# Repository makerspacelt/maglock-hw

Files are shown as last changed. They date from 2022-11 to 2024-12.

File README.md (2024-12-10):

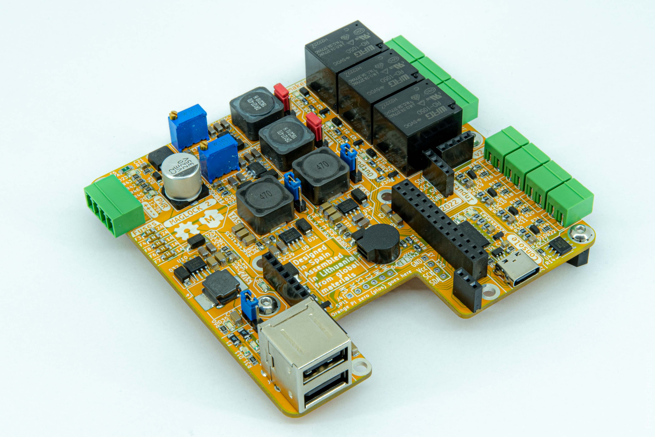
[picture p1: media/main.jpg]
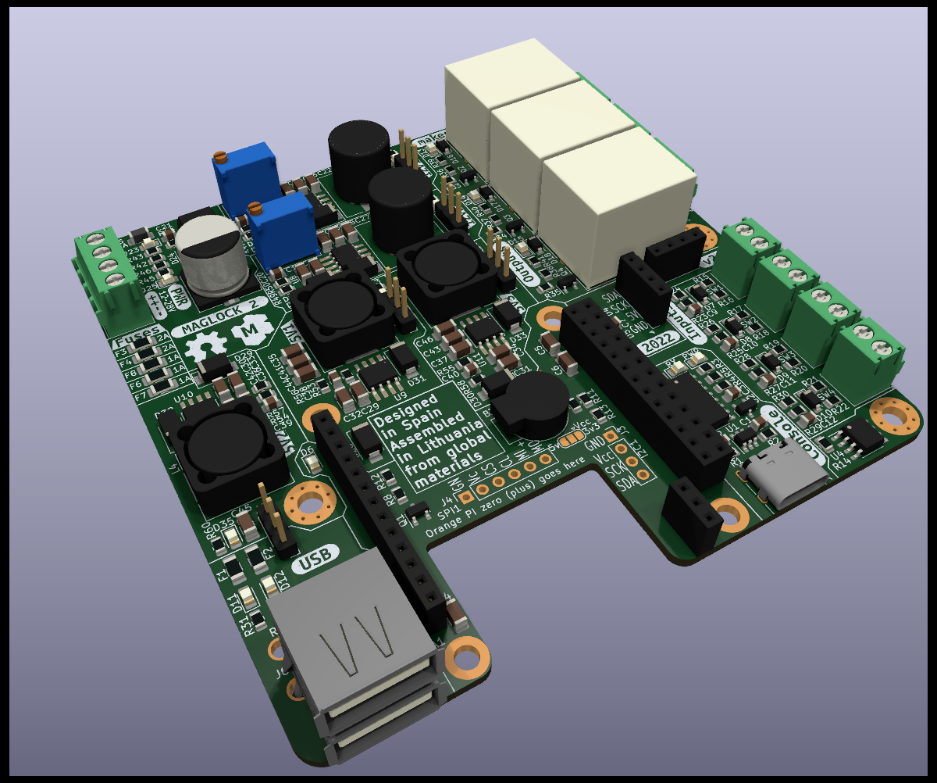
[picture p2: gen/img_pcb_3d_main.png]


MagLock is the entrance controller hardware. It features:

* 2 USB ports for RFID readers
* 3 outputs to electrically controll door (for example, lock/unlock and open/close)
* 4 inputs for normally open switches (for example, doorbell, inside exit button, door position endstops)
* 100Mbps Ethernet for comunication
* onboard UART USB adapter for easy debuging
* onboard DS18B20 1-wire thermometer
* optional I2C oled screen
* additional I2C and SPI breakout for expansion

### Dev NOTEs

* before commit, run `./kibot.sh` to regenerate documentation, bom, gerbers and other assets.
* before fixes after release, bump the version including qr code to next odd value
* before release, bump version to next even value on:
  * every page of schematics and pcb
  * label on front silkscreen
  * qr-code link on bottom silkscreen

* [schematics.pdf](gen/schematics.pdf)
* [pcb.pdf](gen/pcb.pdf)
* [ibom.html](gen/bom_ibom.html)
* [gerbers.zip](gen/gerbers/gerbers.zip)

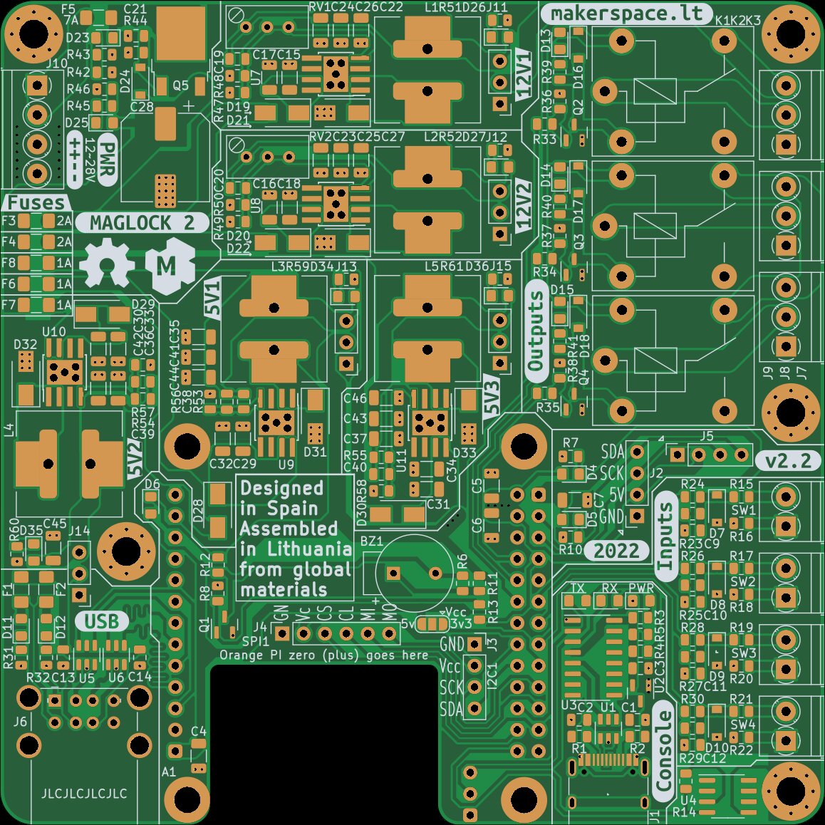
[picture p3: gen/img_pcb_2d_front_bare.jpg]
PCB 2d front bare

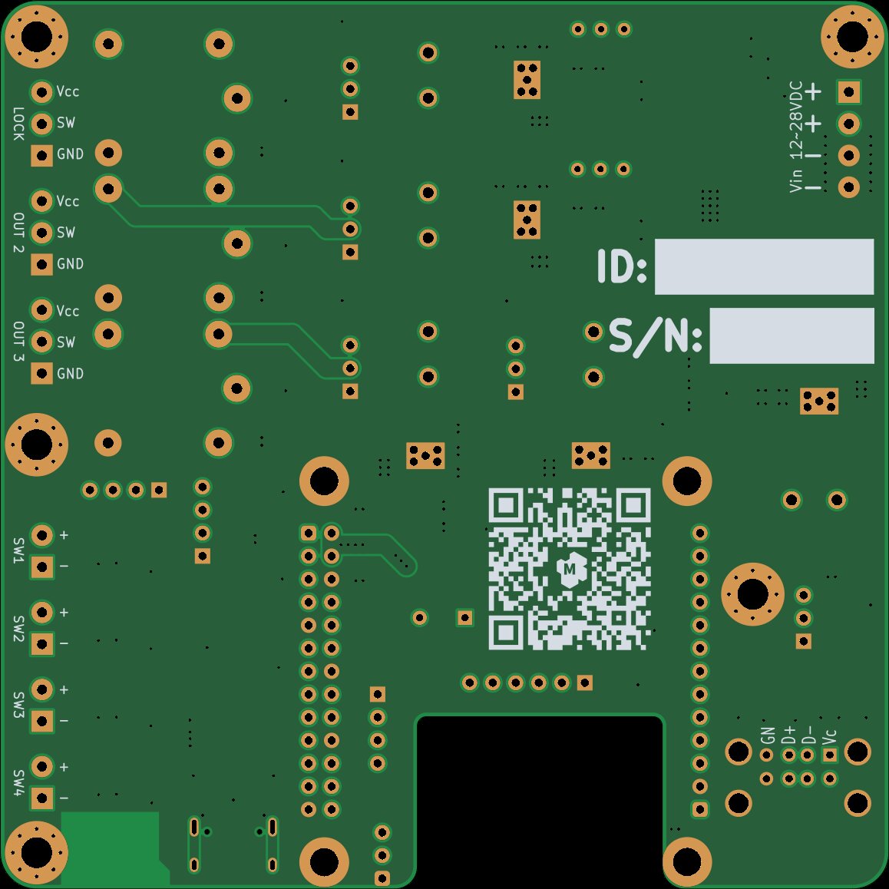
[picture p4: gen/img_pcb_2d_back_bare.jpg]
PCB 2d back bare


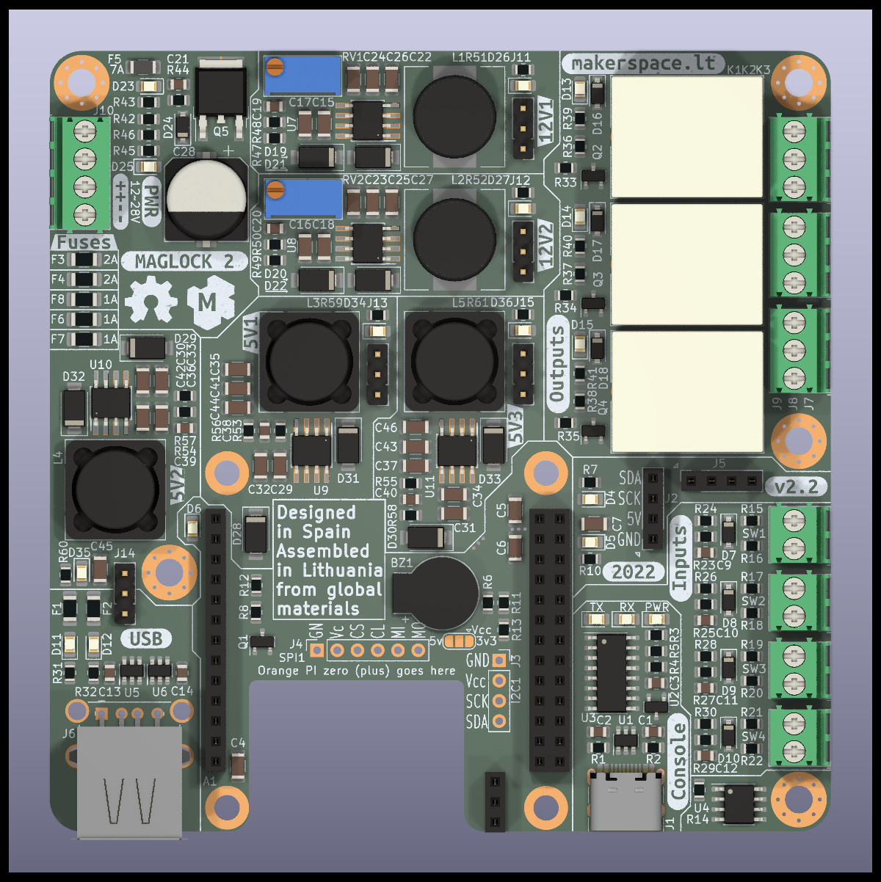
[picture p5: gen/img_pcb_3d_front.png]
PCB 3d front


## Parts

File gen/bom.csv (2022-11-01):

Row | Description | Part | References | Value | Footprint | Quantity Per PCB | Status | Datasheet | LCSC Part Number | WE
1 |  | orange-pi-zero | A1 | orange-pi-zero | Orange_Pi_Zero_LTS | 1 |  | ~ | -
2 | Buzzer, polarized | Buzzer | BZ1 | Buzzer | MagneticBuzzer_CUI_CST-931RP-A | 1 |  | https://datasheet.lcsc.com/lcsc/1810191428_INGHAi-GMD9505RB-3V2700_C252935.pdf | C252935
3 | Unpolarized capacitor | C | C2,C9,C10,C11,C12,C13,C14,C19,C20,C21,C38,C39,C40 | 100n | C_0805_2012Metric | 13 |  | ~ | C161260
4 | Unpolarized capacitor | C | C4,C5,C6,C7,C35,C36,C37,C41,C42,C43,C44,C45,C46 | 100u/10v | C_1206_3216Metric | 13 |  | https://datasheet.lcsc.com/lcsc/1811061115_Murata-Electronics-GRM31CR61A107ME05L_C312983.pdf | C312983 | 885012108012
5 | Unpolarized capacitor | C | C1,C3 | 10u/16v | C_0805_2012Metric | 2 |  | ~ | C77075
6 | Unpolarized capacitor | C | C15,C16,C17,C18,C22,C23,C24,C25,C26,C27,C29,C30,C31,C32,C33,C34 | 10u/35v | C_1206_3216Metric | 16 |  | ~ | C92797 | 885012108022
7 | Polarized capacitor | C_Polarized | C28 | 220u/35v | CP_Elec_10x10 | 1 |  | ~ | C249503 | 875075661007
8 | Zener diode | D_Zener | D7,D8,D9,D10,D24 | 10V | D_SOD-123 | 5 |  | https://datasheet.lcsc.com/lcsc/1806070724_ST-Semtech-MM1Z5240B_C118715.pdf | C118715
9 | 75V 0.15A Fast Switching Diode, SOD-123 | 1N4148W | D16,D17,D18 | 1N4148WL | D_SOD-123 | 3 |  | https://www.vishay.com/docs/85748/1n4148w.pdf | C2908120
10 | Light emitting diode, small symbol, filled shape | LED_Small_Filled | D6,D23 | BLUE | LED_0805_2012Metric_Pad1.15x1.40mm_HandSolder | 2 |  | ~ | C965817
11 | Light emitting diode, small symbol, filled shape | LED_Small_Filled | D2,D3,D13,D14,D15 | GREEN | LED_0805_2012Metric_Pad1.15x1.40mm_HandSolder | 5 |  | ~ | C965815
12 | Light emitting diode, small symbol, filled shape | LED_Small_Filled | D1,D5 | ORANGE | LED_0805_2012Metric_Pad1.15x1.40mm_HandSolder | 2 |  | ~ | C965813
13 | Light emitting diode, small symbol, filled shape | LED_Small_Filled | D4,D11,D12,D34,D35,D36 | RED | LED_0805_2012Metric_Pad1.15x1.40mm_HandSolder | 6 |  | ~ | C965812
14 | 40V 3A Schottky Barrier Rectifier Diode, SMA(DO-214AC) | CDBA340-HF | D19,D20,D21,D22,D28,D29,D30,D31,D32,D33 | SS34A | D_SMA | 10 |  | https://datasheet.lcsc.com/lcsc/2204281430_Guangdong-Hottech-SS34A_C2886580.pdf | C2886580
15 | Light emitting diode, small symbol, filled shape | LED_Small_Filled | D25,D26,D27 | YELLOW | LED_0805_2012Metric_Pad1.15x1.40mm_HandSolder | 3 |  | ~ | C965814
16 | Fuse | Fuse | F6,F7,F8 | 1A | Fuse_1206_3216Metric_Pad1.42x1.75mm_HandSolder | 3 |  | https://datasheet.lcsc.com/lcsc/1912111437_Littelfuse-0466001-NRHF_C151135.pdf | C151135
17 | Fuse | Fuse | F3,F4 | 2A | Fuse_1206_3216Metric_Pad1.42x1.75mm_HandSolder | 2 |  | https://datasheet.lcsc.com/lcsc/1810111821_Littelfuse-0466002-NR_C187595.pdf | C187595
18 | Fuse | Fuse | F5 | 7A | L_1206_3216Metric_Pad1.42x1.75mm_HandSolder | 1 |  | https://datasheet.lcsc.com/lcsc/1809211128_Shenzhen-JDT-Fuse-JFC1206-1700FS_C136352.pdf | C136352
19 | Fuse | Fuse | F1,F2 | PTC 300mA | Fuse_1206_3216Metric_Pad1.42x1.75mm_HandSolder | 2 |  | ~ | C2830239
20 | Generic connector, single row, 01x03, script generated (kicad-library-utils/schlib/autogen/connector/) | Conn_01x03_Male | J11,J12,J13,J14,J15,XJ7,XJ8,XJ9 | 12V_1 | PinHeader_1x03_P2.54mm_Vertical | 8 |  | ~ | ~ C400542
21 | Generic connector, single row, 01x03, script generated (kicad-library-utils/schlib/autogen/connector/) | Conn_01x03_Female | J7,J8,J9 | 3pin | TerminalBlock_Phoenix_PT-1,5-3-3.5-H_1x03_P3.50mm_Horizontal | 3 |  | https://datasheet.lcsc.com/lcsc/1912111437_JILN-JL15EDGRC-35003G01_C409116.pdf | C409116
22 | Generic connector, single row, 01x04, script generated (kicad-library-utils/schlib/autogen/connector/) | Conn_01x04_Female | J2 | I2C0_128x32 | oled_i2c_128x32_ssd1306 | 1 |  | ~ | ~
23 | Generic connector, single row, 01x04, script generated (kicad-library-utils/schlib/autogen/connector/) | Conn_01x04_Female | J5 | I2C0_128x64 | oled_i2c_128x64_ssd1306 | 1 |  | ~ | ~
24 | Generic connector, single row, 01x04, script generated (kicad-library-utils/schlib/autogen/connector/) | Conn_01x04_Female | J3 | I2C1 | PinSocket_1x04_P2.54mm_Vertical | 1 |  | ~ | ~
25 | Generic connector, single row, 01x04, script generated (kicad-library-utils/schlib/autogen/connector/) | Conn_01x04_Female | J10 | Power IN | TerminalBlock_Phoenix_PT-1,5-4-3.5-H_1x04_P3.50mm_Horizontal | 1 |  | https://datasheet.lcsc.com/lcsc/1912111437_JILN-JL15EDGRC-35004G01_C409117.pdf | C409117
26 | Generic connector, single row, 01x06, script generated (kicad-library-utils/schlib/autogen/connector/) | Conn_01x06_Female | J4 | SPI1 | PinSocket_1x06_P2.54mm_Vertical | 1 |  | ~ | ~
27 | USB Type A connector, stacked | USB_A_Stacked | J6 | USB | USB_A_Wuerth_61400826021_Horizontal_Stacked | 1 |  | https://datasheet.lcsc.com/lcsc/2008122034_XUNPU-USB-269-BRW_C720548.pdf | C720548
28 | USB 2.0-only Type-C Receptacle connector | USB_C_Receptacle_USB2.0 | J1 | USB_UART | USB_C_Receptacle_HRO_TYPE-C-31-M-12 | 1 |  | https://datasheet.lcsc.com/lcsc/2205251630_Korean-Hroparts-Elec-TYPE-C-31-M-12_C165948.pdf | C165948
29 | FINDER 36.11, SPDT relay, 10A | FINDER-36.11 | K1,K2,K3 | 5V Relay | Relay_SPDT_Finder_36.11 | 3 |  | https://datasheet.lcsc.com/lcsc/1912111437_WRG-Wangrong-RD-105D_C224434.pdf | C224434
30 | Inductor | L | L1,L2,L3,L4,L5 | 47u/2.5A | L_12x12mm_H8mm__D11.0_P5.0_universal | 5 |  | https://datasheet.lcsc.com/lcsc/2201121400_SHOU-HAN-CYH127-47UH_C2929503.pdf | C2929503 | 744770147
31 | 30V Vds, 5.7A Id, N-Channel MOSFET, SOT-23 | AO3400A | Q1,Q2,Q3,Q4 | AO3400A | SOT-23 | 4 |  | https://datasheet.lcsc.com/lcsc/2204291600_UMW-Youtai-Semiconductor-Co---Ltd--AO3400A_C347475.pdf | C347475
32 | P-MOSFET transistor, gate/drain/source | Q_PMOS_GDS | Q5 | HYG210P06LQ1D | TO-252-2 | 1 |  | ~ | C2834760
33 | Resistor | R | R11,R15,R17,R19,R21 | 0 | R_0805_2012Metric | 5 |  | ~ | ~
34 | Resistor | R | R4,R5,R12,R13,R33,R34,R35 | 330 | R_0805_2012Metric | 7 |  | ~ | ~
35 | Resistor | R | R3,R10,R39,R40,R41,R47,R48,R49,R50 | 1k | R_0805_2012Metric | 9 |  | ~ | ~
36 | Resistor | R | R56,R57,R58 | 1k5 | R_0805_2012Metric | 3 |  | ~ | ~
37 | Resistor | R | R1,R2,R7,R14,R31,R32,R53,R54,R55,R59,R60,R61 | 4k7 | R_0805_2012Metric | 12 |  | ~ | ~
38 | Resistor | R | R6,R8,R16,R18,R20,R22,R36,R37,R38,R42,R43,R44,R45,R46,R51,R52 | 10k | R_0805_2012Metric | 16 |  | ~ | ~
39 | Resistor | R | R23,R24,R25,R26,R27,R28,R29,R30 | 100k | R_0805_2012Metric | 8 |  | ~ | ~
40 | Trim-potentiometer | R_Potentiometer_Trim | RV1,RV2 | 10k | Potentiometer_Bourns_3296W_Vertical | 2 |  | https://datasheet.lcsc.com/lcsc/1811071811_BOCHEN-Chengdu-Guosheng-Tech-3296W-1-103_C118954.pdf | C118954
41 | Generic connector, single row, 01x02, script generated (kicad-library-utils/schlib/autogen/connector/) | Conn_01x02_Female | SW1,SW2,SW3,SW4 | 2pin | TerminalBlock_Phoenix_PT-1,5-2-3.5-H_1x02_P3.50mm_Horizontal | 4 |  | https://datasheet.lcsc.com/lcsc/1912111437_JILN-JL15EDGRC-35002G01_C409115.pdf | C409115
42 | 1A Low Dropout regulator, positive, 3.3V fixed output, SOT-223 | AMS1117-3.3 | U2 | 3V3 LDO | SOT-23 | 1 |  | https://datasheet.lcsc.com/lcsc/1809201825_Shanghai-Siproin-Microelectronics-SSP6206-33NR_C277882.pdf | C277882
43 | USB serial converter, UART, SOIC-16 | CH340G | U3 | CH340C | SOIC-16_3.9x9.9mm_P1.27mm | 1 |  | http://www.datasheet5.com/pdf-local-2195953 | C84681
44 | Programmable Resolution 1-Wire Digital Thermometer SOIC-8 | DS18B20Z | U4 | DS18B20Z | SOIC-8_3.9x4.9mm_P1.27mm | 1 |  | http://datasheets.maximintegrated.com/en/ds/DS18B20.pdf | C695837
45 | Very low capacitance ESD protection diode, 2 data-line, SOT-23-6 | USBLC6-2SC6 | U1,U5,U6 | USBLC6-2SC6 | SOT-23-6 | 3 |  | https://datasheet.lcsc.com/lcsc/1811141711_STMicroelectronics-USBLC6-2SC6_C7519.pdf | C7519
46 |  | XL4001 | U7,U8,U9,U10,U11 | XL4001 | Texas_HTSOP-8-1EP_3.9x4.9mm_P1.27mm_EP2.8x4.1mm_Mask2.8x4.1mm_ThermalVias | 5 |  | https://datasheet.lcsc.com/szlcsc/XL4001E1_C73347.pdf | C2988027
47 | Generic connector, single row, 01x04, script generated (kicad-library-utils/schlib/autogen/connector/) | Conn_01x04_Male | XJ10 | 4pin |  | 1 |  | ~ | C393014
48 | Generic connector, single row, 01x01, script generated (kicad-library-utils/schlib/autogen/connector/) | Conn_01x01_Female | XJaA1,XJbA1,XJcA1 | Conn_02x13_Female_2.54 |  | 3 |  | ~ | C350298 C52709 C2935974
49 | Generic connector, single row, 01x02, script generated (kicad-library-utils/schlib/autogen/connector/) | Conn_01x02_Male | XSW1,XSW2,XSW3,XSW4 | 2pin |  | 4 |  | https://datasheet.lcsc.com/lcsc/1912111437_JILN-JL15EDGK-35002G01_C393013.pdf | C393013

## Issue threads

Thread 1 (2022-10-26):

Q5 - wrong pinout of reverse voltage protection P-FET

dariuskt, 2022-10-26:
in schematics Q5 symbol is ok, but pin numbers 2 and 3 should be swapped.

Closed 2022-11-01.

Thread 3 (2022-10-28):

BZ1 - wrong footprint hole spacing

dariuskt, 2022-10-28:
hole spacing should be 5mm

Closed 2022-11-01.

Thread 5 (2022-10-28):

LEDs driven from 5V rail are too bright

dariuskt, 2022-10-28:
use 4k7 current limiting resistor for all LEDs driven from 5V. including:

* PSU outputs (R59,R60,R61)
* USB power (R31,R32)
* relay outputs (R39,R40,R41)

dariuskt, 2022-11-01:
relay outputs can be left bright as they represent door status that might be interesting to the user

Closed 2022-11-01.

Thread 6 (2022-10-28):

R{7,9} - superfluous current limiting resistors

dariuskt, 2022-10-28:
replace R7 and R9 with a single 4k7 resistor

Closed 2022-11-01.

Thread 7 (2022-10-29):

U{7..11} - thermal vias too small

dariuskt, 2022-10-29:
enlarge thermal vias and remove a bit of silkscreen from the back

Closed 2022-11-01.

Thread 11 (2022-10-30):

R{15,17,19,21} - prevents button press detection by not pulling signal down enough

dariuskt, 2022-10-30:
replace R{15,17,19,21} with zero ohm links. R{16,18,20,22} should be enough for the current limiting.

Closed 2022-11-01.

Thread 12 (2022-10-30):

D{7..10} - zener leakage current is too high - prevents button press detection

dariuskt, 2022-10-30:
with 100k pull-up to 3v3 zener pulls voltage down to 1.3v
possibly use a higher voltage zener, for example, 12v.

Closed 2022-11-01.

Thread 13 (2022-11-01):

D24 - reverse voltage protection FET gate clamping is too low

dariuskt, 2022-11-01:
replace D24 with a higher voltage zener, for example, 12V.

Closed 2022-11-01.

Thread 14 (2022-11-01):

R44 - reverse voltage protection FET gate pull-down is too weak

dariuskt, 2022-11-01:
make R44 a 10K resistor. the power dissipation still should be within spec for the full Vcc range and gate driving should be more resistant to zener leakage current.

Closed 2022-11-01.

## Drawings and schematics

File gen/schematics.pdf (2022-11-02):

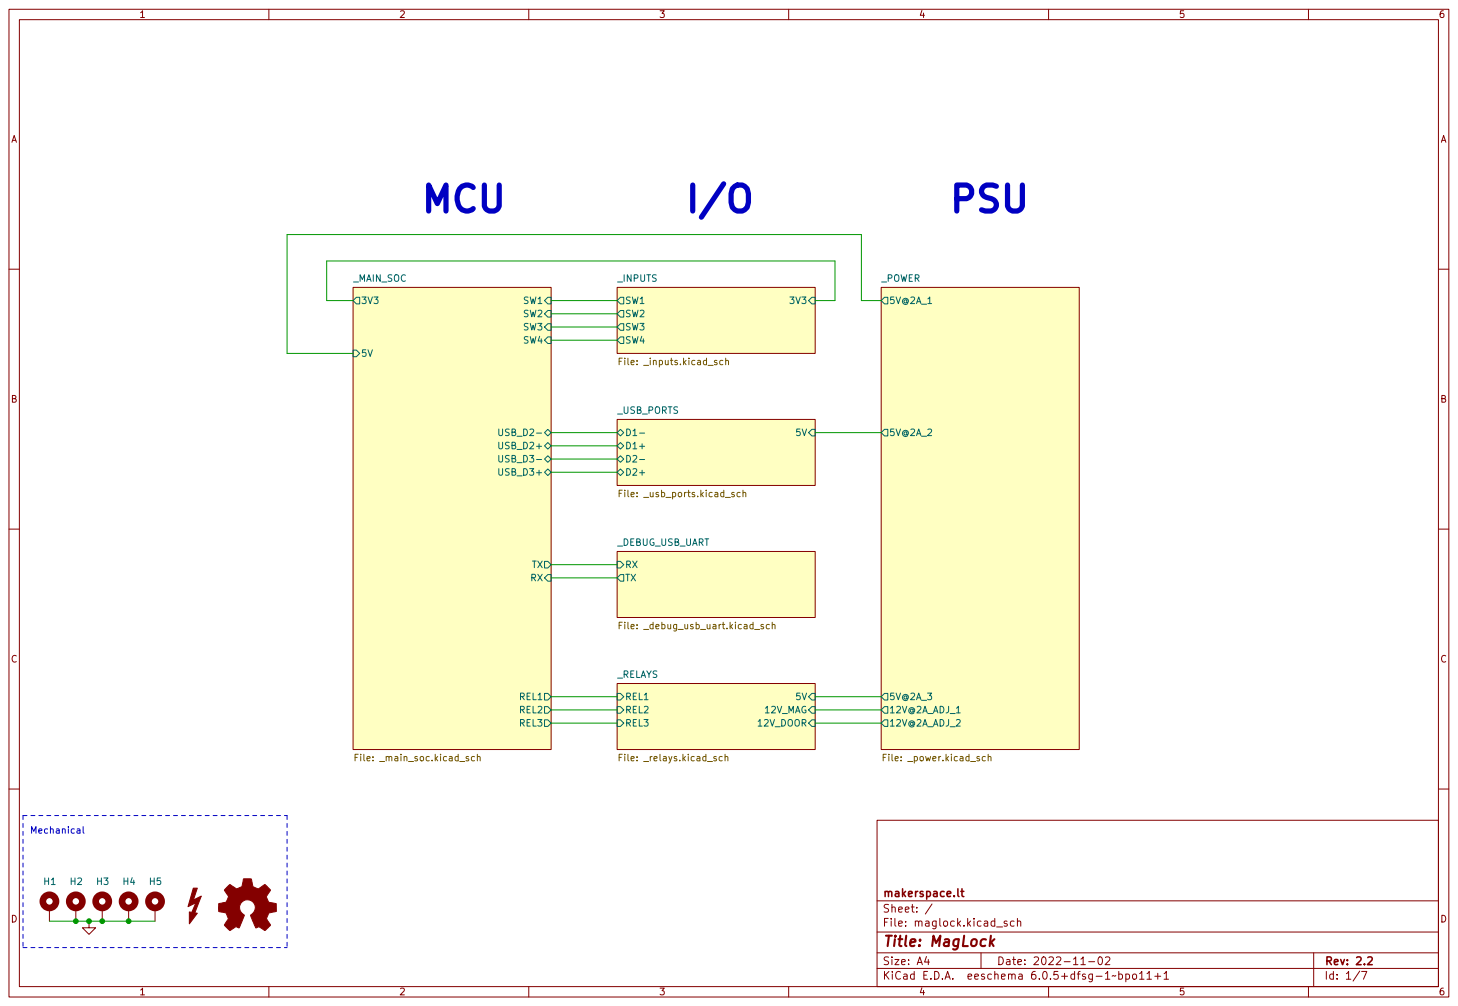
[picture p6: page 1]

File: maglock.kicad_sch Sheet: / makerspace.lt

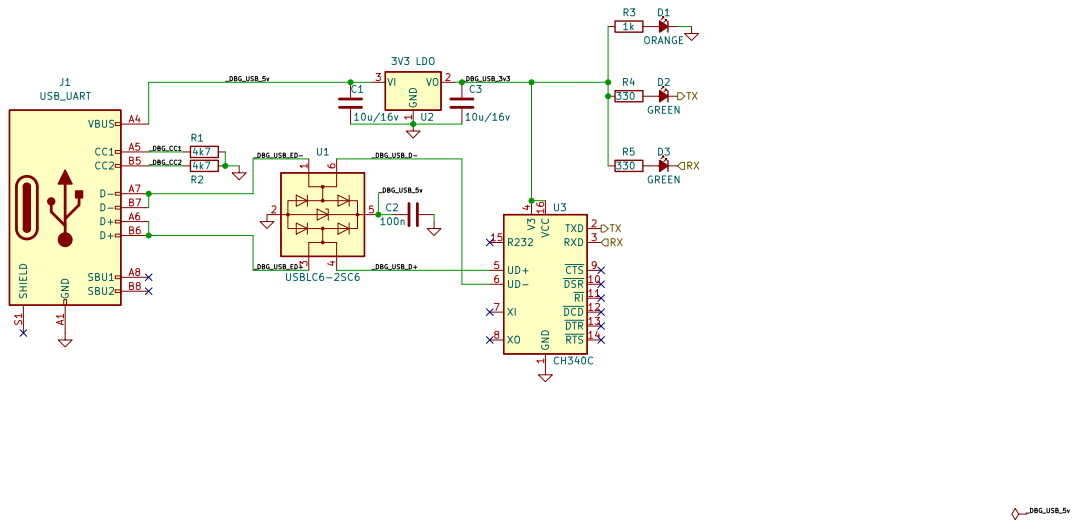
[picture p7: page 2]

1 ~{DSR}10 ~{RI}11 ~{DCD}12 ~{DTR}13 ~{RTS}14 R232 15 VCC 16 TXD 2 RXD 3 V3

4 UD+ 5 UD- 6 XI 7 XO 8 ~{CTS} 9 U3CH340C

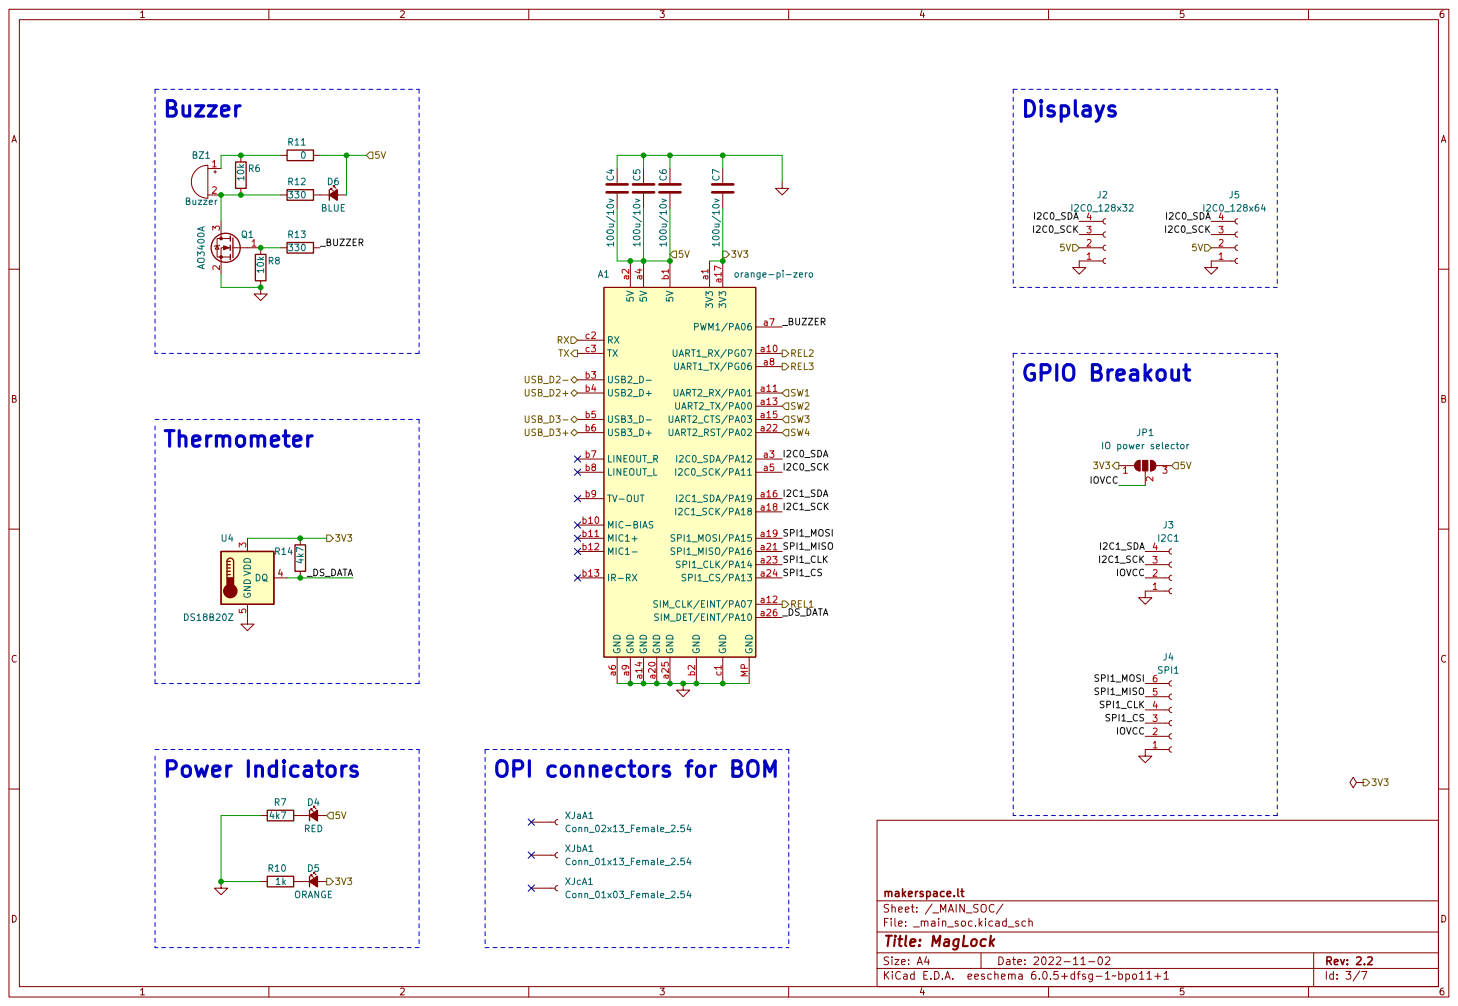
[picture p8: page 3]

OPI connectors for BOM

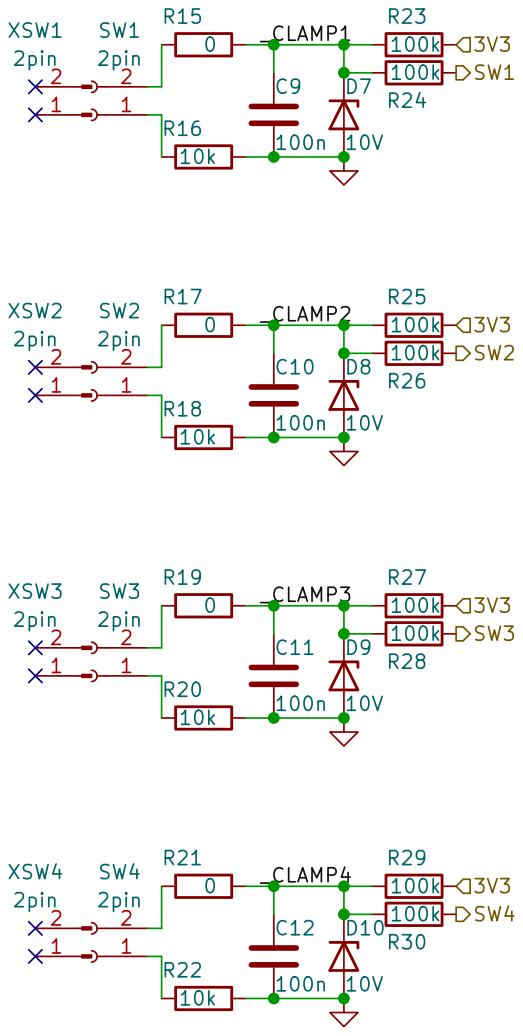
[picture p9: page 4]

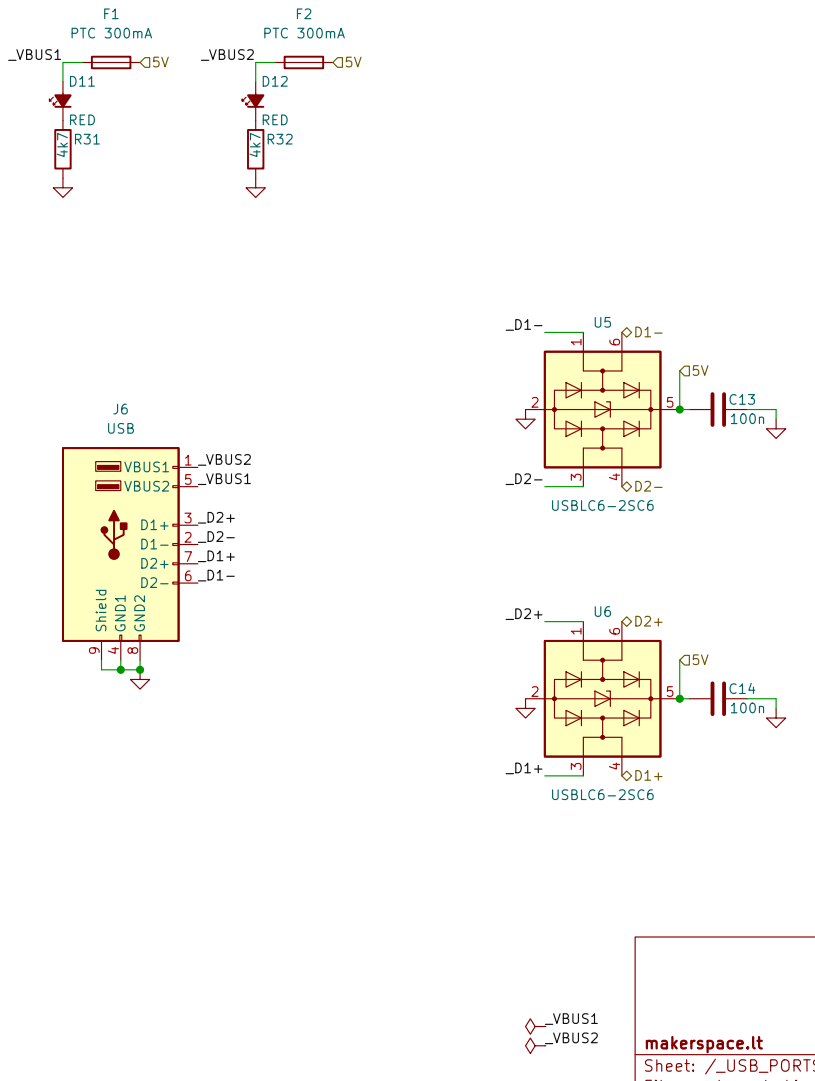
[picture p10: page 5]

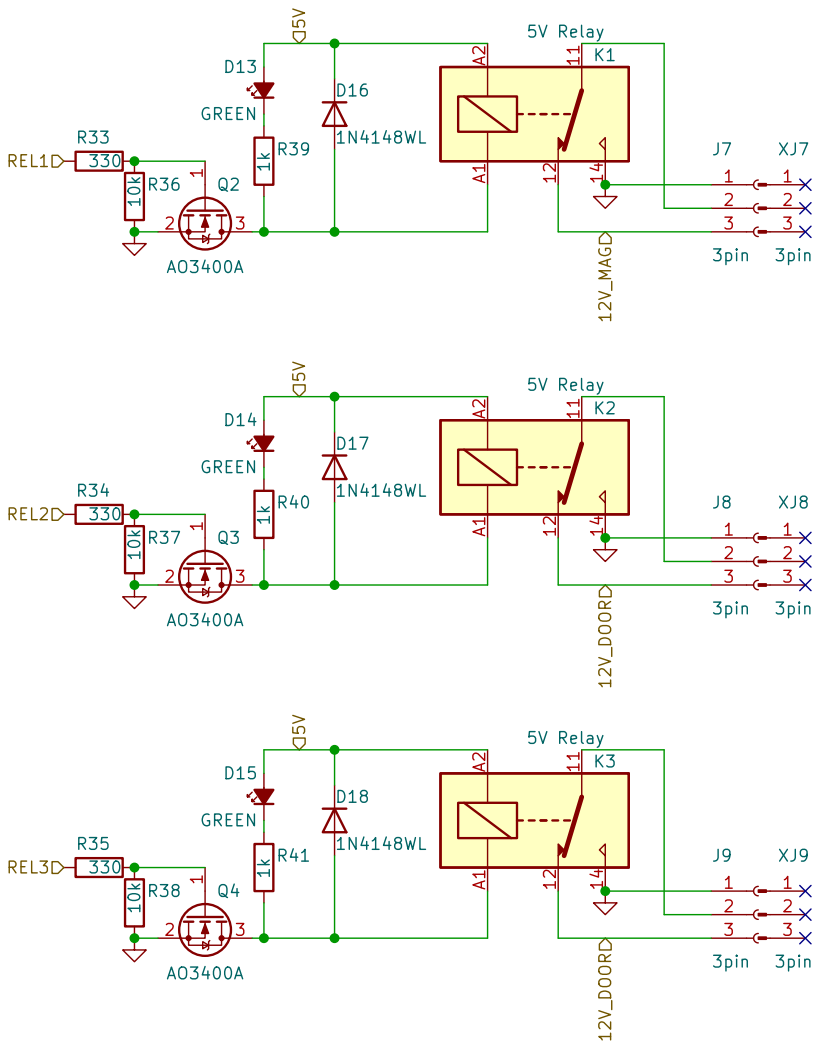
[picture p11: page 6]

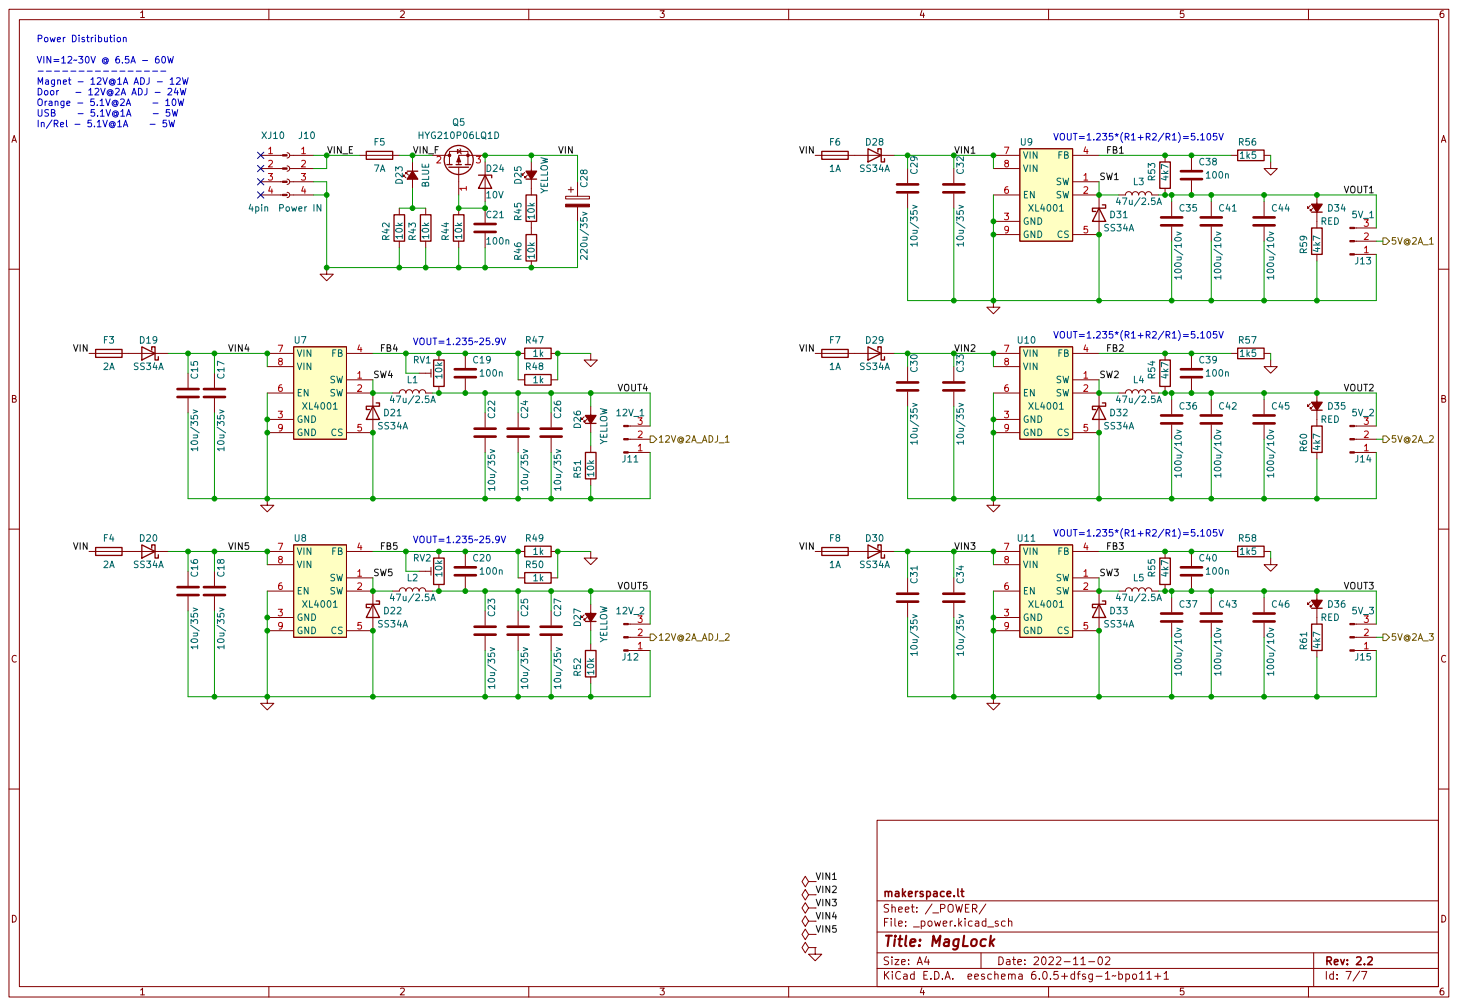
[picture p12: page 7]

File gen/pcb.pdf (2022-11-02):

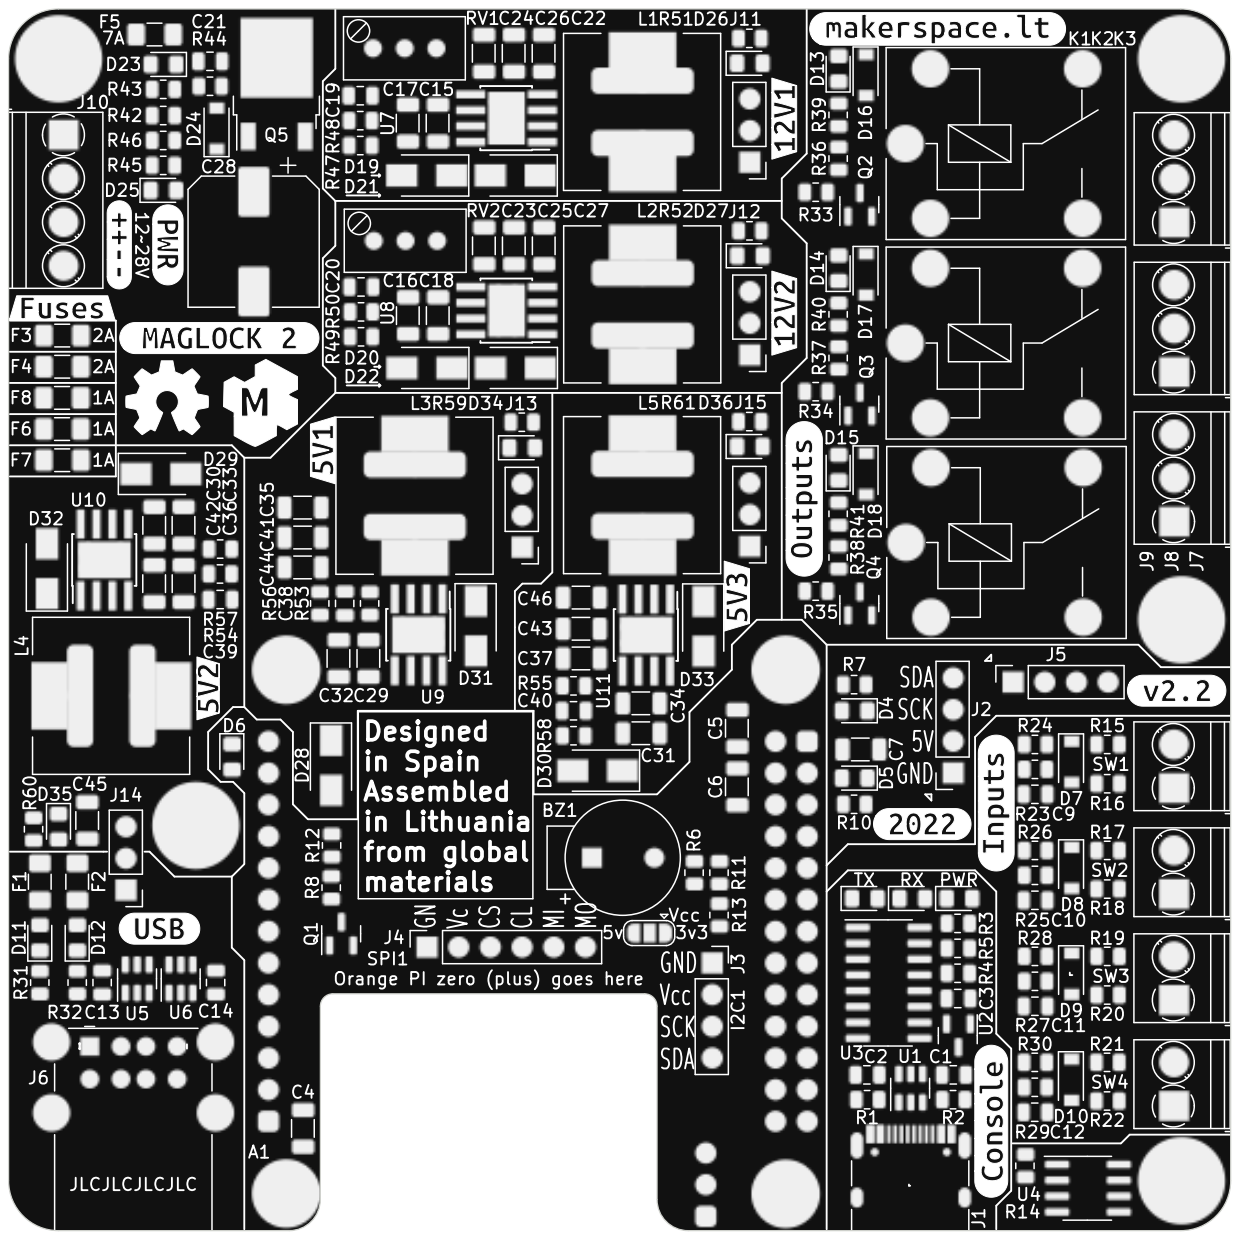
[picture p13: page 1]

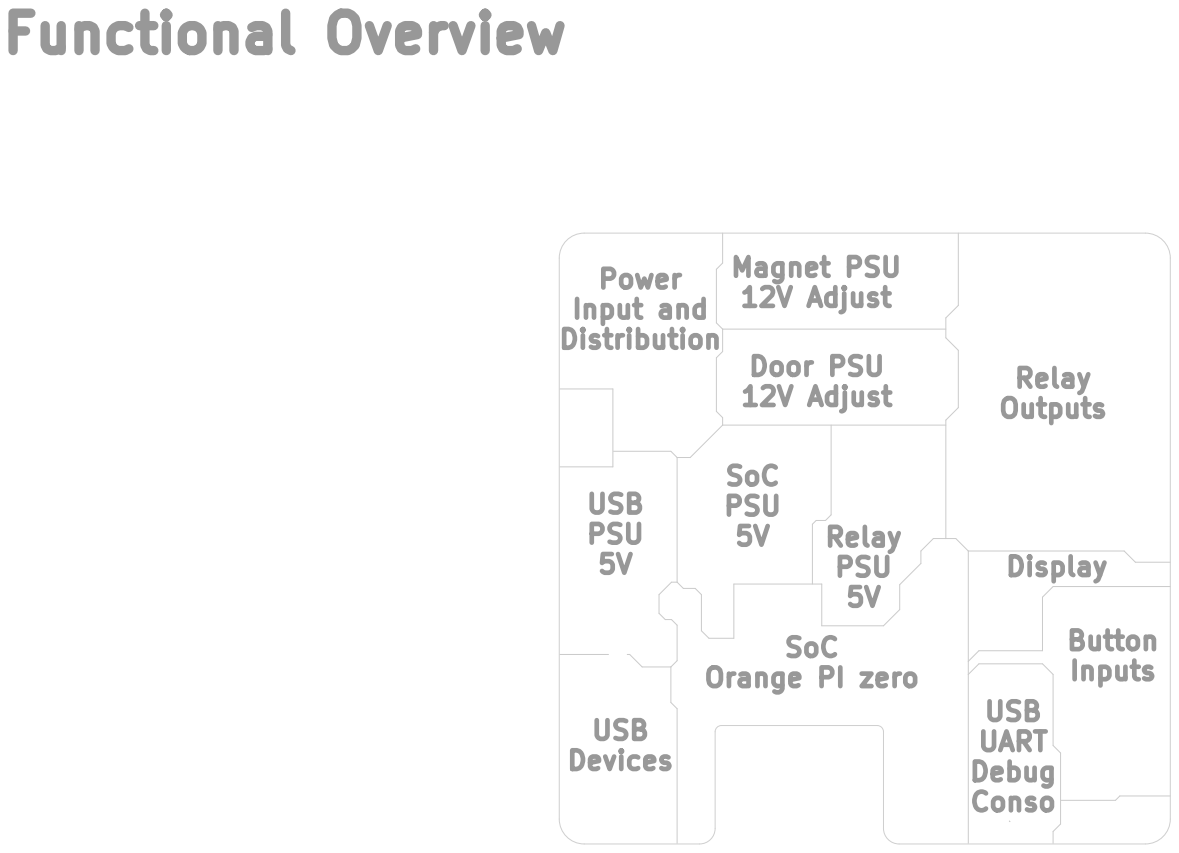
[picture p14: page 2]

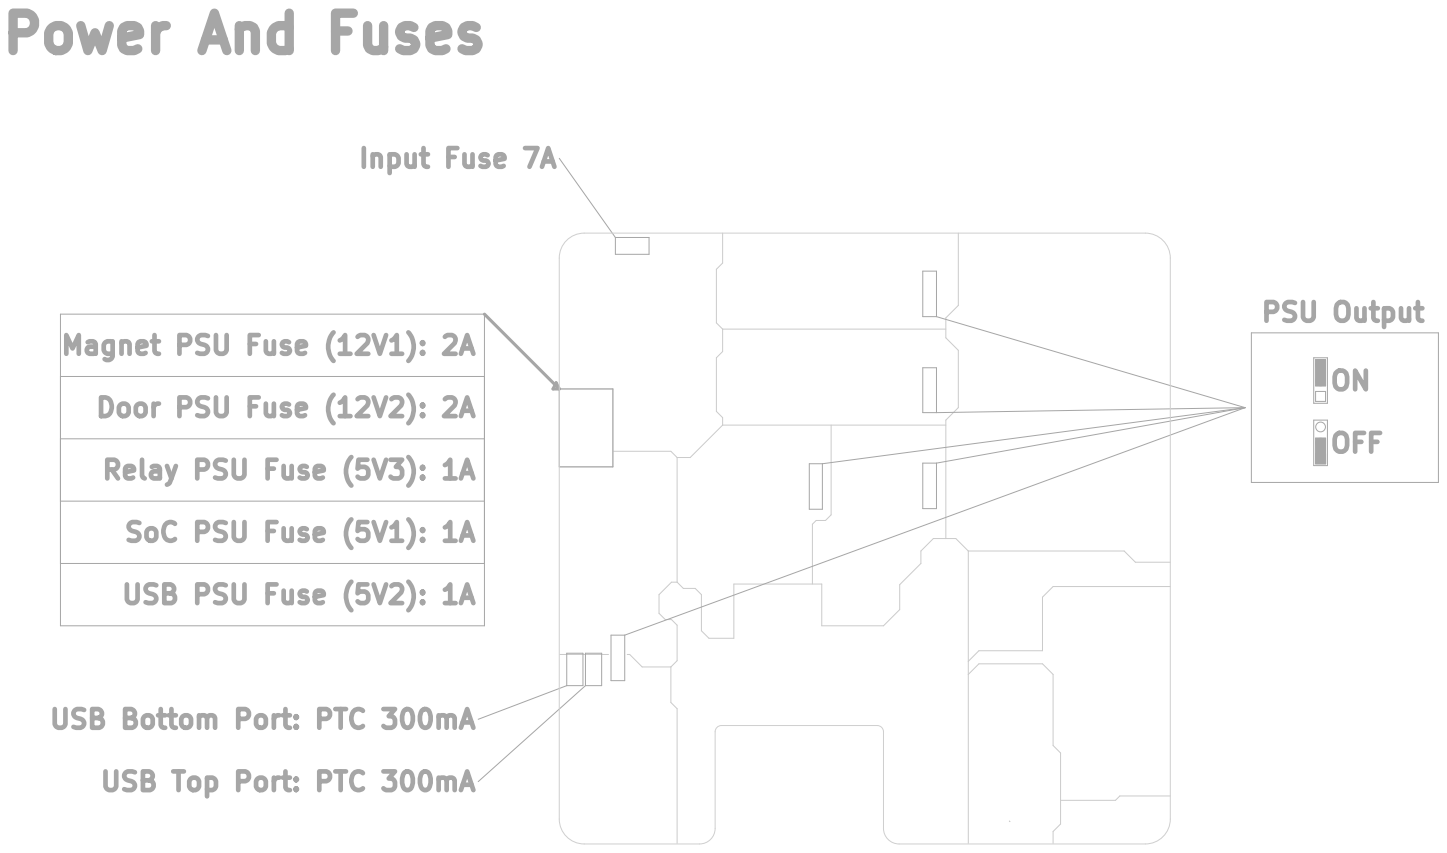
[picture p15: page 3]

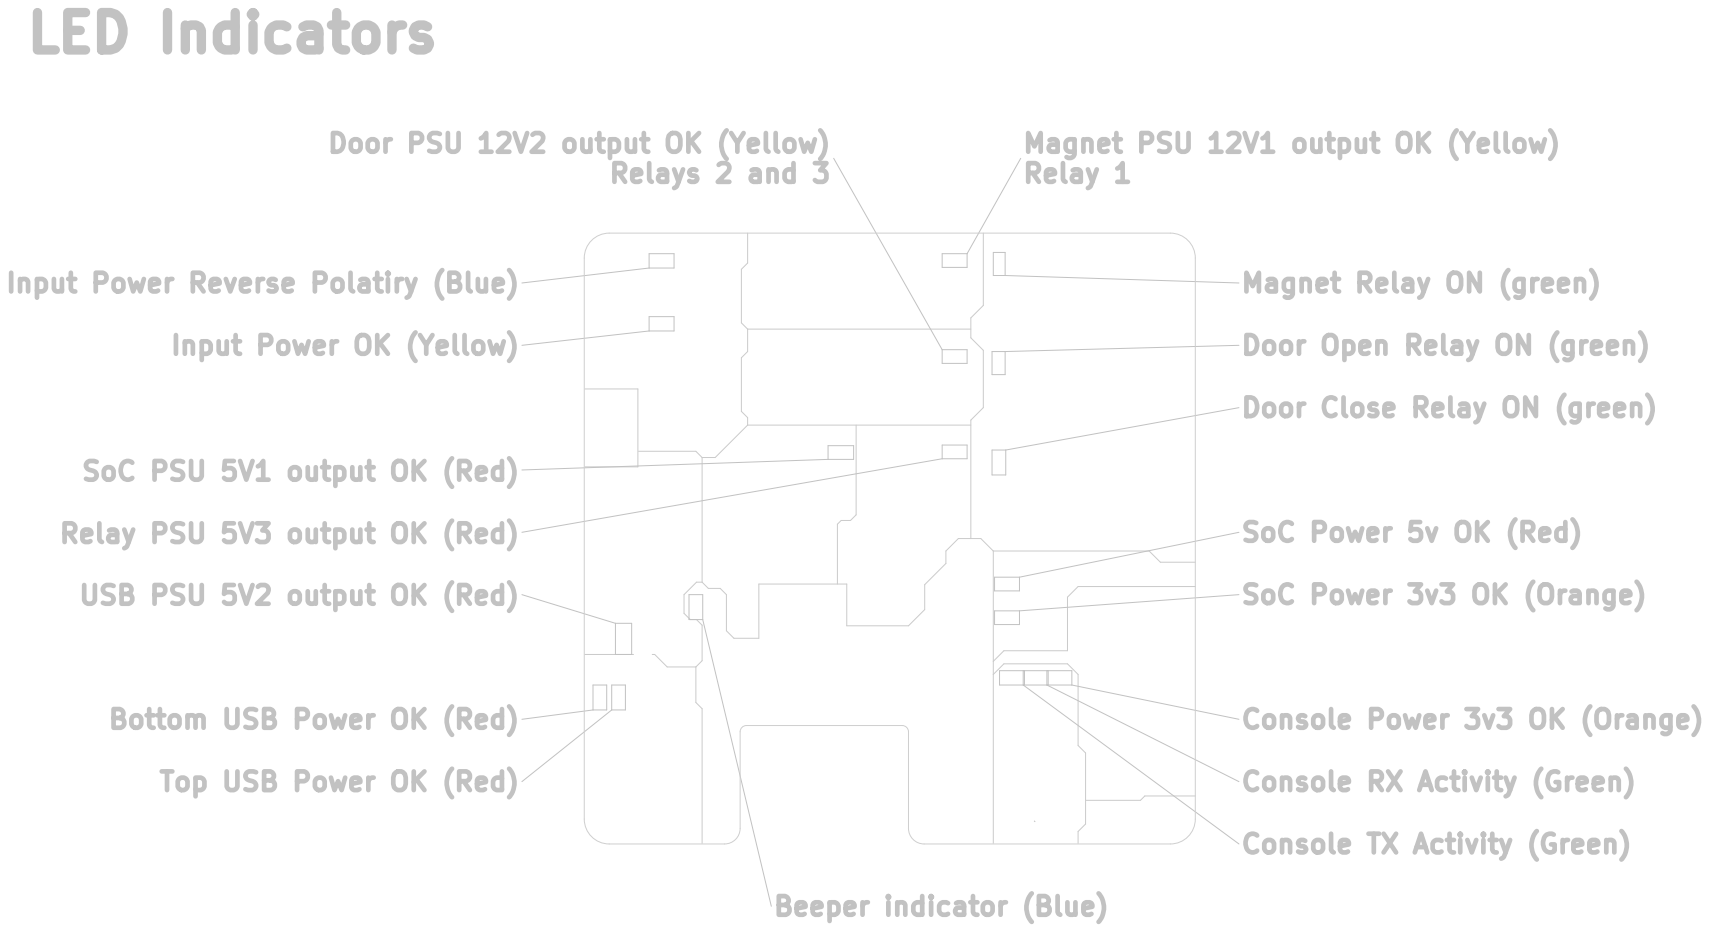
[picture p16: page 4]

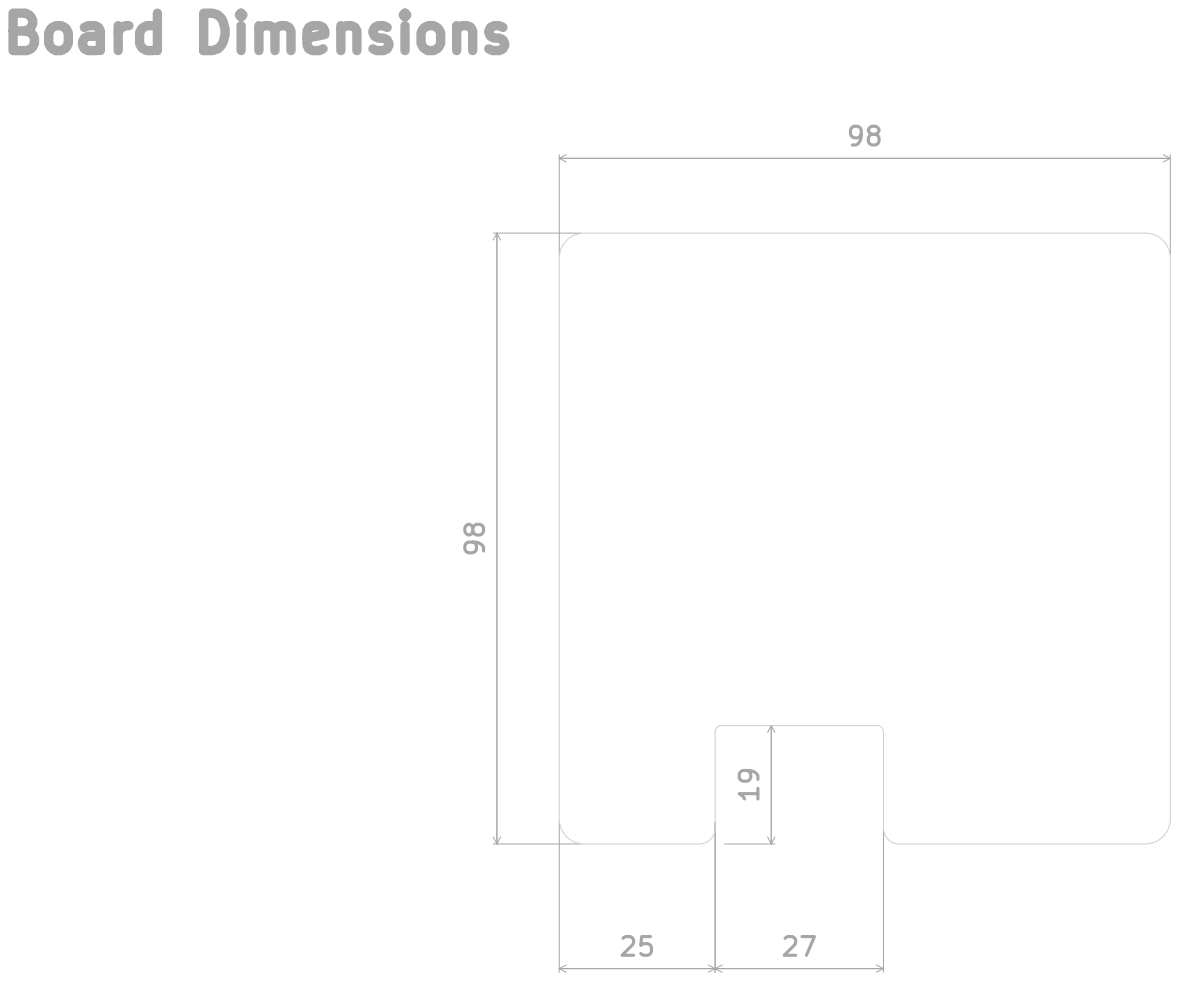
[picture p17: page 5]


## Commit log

2022-07-13 adding project WIP
    [_debug_usb_uart.kicad_sch, _inputs.kicad_sch, _main_soc.kicad_sch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]
2022-07-16 most stuff squeezed on board
    [_inputs.kicad_sch, _main_soc.kicad_sch, _power.kicad_sch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]
2022-07-17 general routing finished
    [_debug_usb_uart.kicad_sch, _inputs.kicad_sch, _main_soc.kicad_sch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]
2022-07-18 adding more info to silkscreen
    [_main_soc.kicad_sch, maglock.kicad_pcb]
2022-07-18 adding documentation layers
    [_inputs.kicad_sch, _power.kicad_sch, _relays.kicad_sch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]
2022-07-18 adding usb port 3d model
    [_usb_ports.kicad_sch, maglock.kicad_pcb, maglock.kicad_sch]
2022-07-18 ERC, DRC and BOM fixes
    [_debug_usb_uart.kicad_sch, _inputs.kicad_sch, _main_soc.kicad_sch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]
2022-07-18 bom and documentation fixes
    [_debug_usb_uart.kicad_sch, _power.kicad_sch, _relays.kicad_sch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]
2022-07-19 updating qr link to include version
    [maglock.kicad_pcb]
2022-07-19 adding project info to sheet frames
    [_debug_usb_uart.kicad_sch, _inputs.kicad_sch, _main_soc.kicad_sch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]
2022-07-19 adding documentation, bom and production files
    [bom.csv, bom_lcsc.csv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]
2022-11-01 adding pre/post release checklist and preparing for fixes
    [_debug_usb_uart.kicad_sch, _inputs.kicad_sch, _main_soc.kicad_sch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]
2022-11-01 adding direction markers for pots. fixes #2
    [_power.kicad_sch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]
2022-11-01 adding direction marker for buzzer. fixes #4
    [_main_soc.kicad_sch, maglock.kicad_pcb, maglock.kicad_sch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]
2022-11-01 moved S/N and ID fields away from vias. fixes #8
    [maglock.kicad_pcb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]
2022-11-01 removing unreadable text from OSHW logo. fixes #15
    [maglock.kicad_pcb, maglock.kicad_sch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]
2022-11-01 adding OPI connectors to lcsc BOM. fixes 9
    [_main_soc.kicad_sch, bom.csv, bom_lcsc.csv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]
2022-11-01 making buzzer louder by using 0R in place of current limiter. fixes #10
    [_main_soc.kicad_sch, bom.csv, maglock.kicad_sch]
2022-11-01 driving Q5 harder by decreasing R44 resistance. fixes #14
    [_power.kicad_sch, bom.csv, maglock.kicad_sch]
2022-11-01 pulling signal lower on button press. fixes #11
    [_inputs.kicad_sch, bom.csv, maglock.kicad_sch]
2022-11-01 reducing PSU and USB power LEDs brightness. fixes #5
    [_power.kicad_sch, _usb_ports.kicad_sch, bom.csv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]
2022-11-01 fixing hole spacing in the buzzer footprint. fixes #3
    [_main_soc.kicad_sch, _relays.kicad_sch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]
2022-11-01 removing an unnecessary resistor from OPI 5V indicator. fixes #6
    [_main_soc.kicad_sch, bom.csv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]
2022-11-01 improving lx4001 footprint thermals. fixes #7
    [_main_soc.kicad_sch, _power.kicad_sch, bom.csv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]
2022-11-01 using 10V zeners instead of 3V3 in all places. fixes #12, fixes #13
    [_inputs.kicad_sch, _power.kicad_sch, bom.csv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]
2022-11-01 fixing Q5 footprint and rerouting. fixes #1
    [_power.kicad_sch, bom.csv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]
2022-11-01 tidying up silkscreen
    [maglock.kicad_pcb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]
2022-11-02 bumping up version to 2.2 for production
    [_debug_usb_uart.kicad_sch, _inputs.kicad_sch, _main_soc.kicad_sch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]
